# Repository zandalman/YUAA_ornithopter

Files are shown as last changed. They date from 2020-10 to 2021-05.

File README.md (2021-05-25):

# YUAA Ornithopter Project

An ornithopter is a flying machine that generates thrust and lift by imitating the flight of birds. Ornithopters have the advantages of maneuverability, versatility, and stealth over traditional aircraft, making them useful in aerial reconnaissance, search & rescue, and agricultural surveying. In this project, we design and build an ornithopter capable of sustained flight and maneuvering.

# Software

## Controls

Our ornithopter is highly customizable, with many adjustable variables to cater to various flying styles. Such include:

 - **maxFrequency**: Maximum flapping frequency reached when throttle is pulled all the way up. The higher the value, the faster the wings flap, and the more sensitive the flapping frequency will be.
 - **zeroThrottleAngle**: Our ornithopter glides when the throttle is set to 0, or a range close to 0 denoted by **deadZone**. This variable adjusts the angle (in degrees) above the horizontal the wing rests at in glide mode.
 - **levelAngle**: Angle above the horizontal at center of flapping cycle.
 - **maxAmplitude**: How far above and below **levelAngle** the wing flaps.
 - **maxRollPhaseShift**: Roll is achieved by adding a phase delay to the wing opposite to the side of which you want to turn. This variable defines the maximum phase shift when the magnitude of the roll control is at its maximum.
 - **maxPitchAngle**: Pitch is elevated by raising the **levelAngle** and lowered by decreasing it. This variable denotes the maximum change to **levelAngle** when pitch is set to its maximum magnitude. The higher this is, the more sensitive the pitch control.
 - **maxYawAngle**: Yaw is achieved by lowering the **levelAngle** on the side you yaw towards and raising it on the opposite side. This variable defines the maximum deviation to **levelAngle** when yaw is set to its maximum magnitude. The higher this is, the more sensitive the yaw control.
 - **deadZone**: For every control, there is a range in which the value is interpreted as 0. This allows for gliding and makes it easy to keep a purely level angle. The higher this value is, the larger that dead zone.
 - **delayTime**: Frequency at which a new control is registered and a new servo output is generated. The lower this is, the smoother the controls.

All other parameters should be left unmodified.

## Behind the Scenes

The remote controller has 8 channels, each mapped to a control (roll, pitch, yaw, etc.). For each of the controls, we normalize the digital input to a value between 0 and 1 or -1 and 1. There are three control modes—normal, amp, and basic—that reconfigure the layout of the controls. Every iteration of the event loop, we input the controls into a function called **updatePosition()**, which renders new servo positions corresponding to the positions in the flap cycle. **updatePosition()** is a void function, meaning it directly updates the global variables instead of returning an output. The function relies on a unit circle methodology, where the wing position is the *sin* of a rotating point around a circle, and the linear velocity of the rotating point is determined by the throttle. The other controls module the angle and phase.

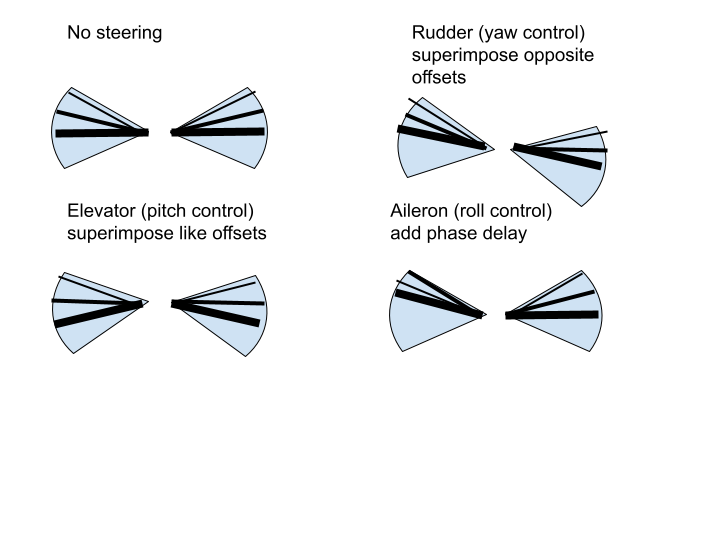
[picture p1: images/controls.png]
Controls


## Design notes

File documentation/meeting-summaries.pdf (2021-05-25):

09/20/2020

Group members
- Zack (project leader)
- Theo
- Kai
- Elijah
- … others???

CAD
- We will probably use Autodesk 360
- Collaborative
- Integrates with Autodesk Eagle
- Okay if you don’t have CAD experience; we will teach you

About the ornithopter
- Wingspan will be in the 1’ to 2’ range
- Steering will be done using a tail wing

Ornithopter kits
- We will send out ornithopter kits some time this month
- See ornithopter kits document for kit options
- Open for ideas for personalized kits because the group is relatively small
- We could also start with designing a more custom kit to send

Design questions to answer as a group
- Gearbox vs servos
- Gearbox
■ More mechanically inclined project ■ More power
- Servos
■ More programming inclined project ■ More control/maneuverability

09/26/2020

See the slides titled “Design Considerations”

New group members
- Olivia

How do ornithopters fly?
- Downstroke

- Wings twist to maintain angle of attack for providing thrust
- Upstroke
- Outer wing lies parallel to direction of motion to minimize resistance
- Inner wing still generates lift

Rudimentary sketch

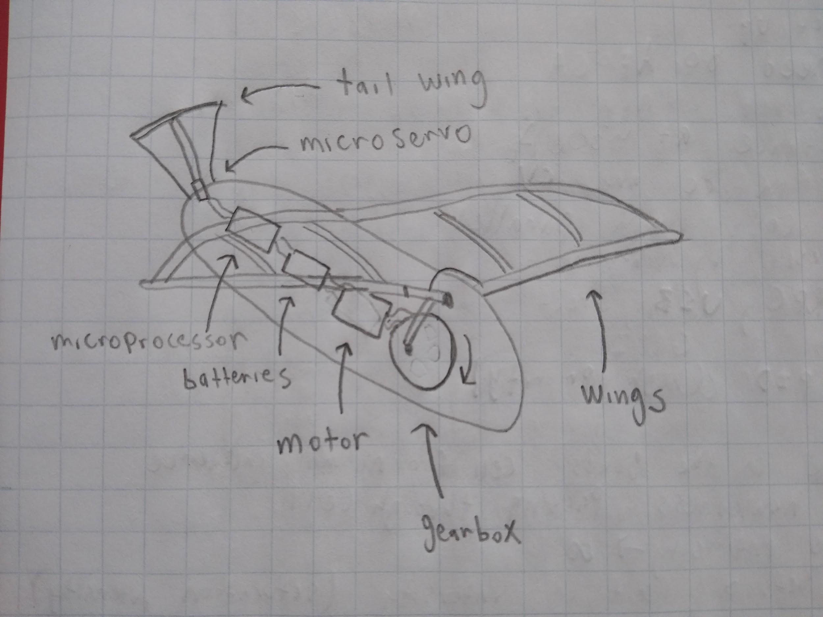
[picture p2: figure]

Electrical components
- Microcontroller (Arduino nano)
- LiPo battery
- Servo
- Brushless motor
- Electronic speed control (ESC)

Mechanical components
- Wing spar (carbon fiber)
- Wings (ripstop or nylon)
- Gear box (transverse gear shaft)
- Frame (carbon fiber)

Kits
- Olivia wants the electronics kit

Tasks

- Olivia will look into necessary software
- Theo will mock up a gear design

Meetings
- We probably need to find a better meeting time
- Weekday schedules are more consistent than weekend schedules

General plans
- Each person will build their own basic ornithopter from kits
- Then we will each work on parts of the preliminary design
- Over winter break, we will consolidate the parts into a full ornithopter

10/04/2020

New group members
- Elsa Durcan
- Bill

Installing Autodesk Fusion 360
1. Go to this link. (https://www.autodesk.com/education/edu-software/overview?sorting=featured&page=1)
2. Click ‘Get Started.’
3. Follow the steps to create an Autodesk account.
4. Install Autodesk Fusion 360 and log in with your account information.
5. Let me know your email so that I can invite you to join the ornithopter project.

Design considerations
- We have decided on the servo method ornithopter

Budget
- We have a lot of money
- ~$3000
- We shall spare no expense!

Materials to send out
- Arduino kit
- Micro servos
- Materials to build the Freebird ornithopter (see resources page)
- Should be able to get materials to everyone in ~2 weeks

Tasks
- Servo software
- Create the Arduino software that will control the wing servos
- Electronics

- Use Autodesk Eagle to design a custom PCB
- Arduino nano
- Gyroscope
- Servos
- Frame
- Create a lightweight ornithopter frame
- Initial prototypes will be 3D printed, but later carbon fiber
- Servos and electronics should mount to frame
- Wing design
- Material
- Wing shape
- Where to place wing spars
- Simulation
- Aerodynamics simulations
- Analytical models
- Testing
- Design a testing rig for future prototypes
- Ornithopter attaches to lever arm for testing thrust
- Force sensor for testing lift

Sorry that I sounded like I was dying today!

10/11/2020

New group members
- Erick

Github
- We have a project github (https://github.com/zandalman/YUAA_ornithopter)
- Commit often and with meaningful messages
- Let me know if you don’t know how to use github and I can teach you

Freebird ornithopter
- Watch video in resources tab
- Parts will hopefully arrive in 1-2 weeks

Parts
- We will probably use
- Servo (https://www.servocity.com/hsb-9370th-servo/)
- RC controller
(https://www.racedayquads.com/products/flysky-fs-i6-6ch-2-4ghz-rc-transmitter-w-ia6-rx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 (https://www.racedayquads.com/products/flysky-fs-i6-6ch-2-4ghz-rc-transmitter-w-ia6-rx?variant=31607739383921)

VjFQtWn2D6Cq5RWLeTxrtjhKH7ACsuyGcYTnIrtvQOSKdmMEaAvhNEALw_wc
B) (https://www.racedayquads.com/products/flysky-fs-i6-6ch-2-4ghz-rc-transmitter-w-ia6-rx?variant=31607739383921)
- Accelerometer/gyroscope (https://www.adafruit.com/product/4692)

Simulation
- Still need to decide simulation software
- Matlab/simulink (https://www.mathworks.com/help/aeroblks/aerodynamics.html)
- Autodesk CFD
(https://www.autodesk.com/products/cfd/overview?_ga=2.186200874.2037225500.1602 442768-2115175104.1601829206) (https://www.autodesk.com/products/cfd/overview)
- SimScale
(https://www.autodesk.com/products/fusion-360/blog/simscale-launches-engineering-simulation-integration-autodesk-fusion-360/) (https://www.autodesk.com/products/fusion-360/blog/simscale-launches-engineering-simulation-integration-autodesk-fusion-360/)

One-on-one meetings
- If you have any questions or don’t know how to do something, we can arrange a 1-on-1 meeting
- Or if its something quick you can just messages me

Task channels
- Each task has its own channel in the Discord
- Use task channel to collaborate on tasks

Starter task assignments
- Olivia - software
- Bill - electronics
- Erick - wings
- Elsa - frame
- Kai - simulation

10/18/2020

Grant applications
- See in Google Drive
- Examples in case you are interested in becoming a YUAA project leader at some point

Electronics
- 5 V LiPo battery will last longer than a 9 V LiPo battery and will not require a regulator

Simulation
- AmSys and SimScale both provide educational licenses
- SimScale is hosted online and is more lightweight
- SimScale may be better for our purposes

- STP files are a universal 3D model file format that will probably work between different softwares

Parts
- We can finally order parts for the ornithopter
- Will send rubber band powered ornithopter parts to everyone
- Will send Arduino kit to everyone
- Will Bill teensy and gyroscope
- Will send Olivia servo arm, gyroscope, and RC controller
- Will send Erick carbon fiber wing spars

10/25/2020

General
- Reach out to me to set up a one-on-one meeting about advice for your specific task

Grants
- CT Space Grant submitted!

YUAA Talk
- Upcoming YUAA talk at 6 pm EST, Friday November 6th by NASA engineer Brandon Lloyd

Arduino Kits
- Arduino kits have arrived
- Distributing Arduino kits at 4 pm today at Cross Campus
- Unboxing video
- Kit includes Arduino, multimeter, USB cable, breadboard, battery, resistors, micro servo, and more
- Remember to always measure voltage in parallel and current in series with the multimeter
- Recommend trying LED tutorial to get used to Arduino https://www.arduino.cc/en/Tutorial/BuiltInExamples/Blink

Electronics
- Either attach RC receiver directly to the PCB or attach it with an IDC cable
- Gyroscope must use SDA and SCL ports on Arduino, only ports which support I2C protocol
- Will order RC system and gyroscope soon

Simulation
- Generative design is built into Fusion and will be useful for modelling wings
- Look into various wing shapes and wing spar layouts

- Possible meeting with Larry Wilen to discuss aerodynamics

11/01/2020

YUAA Talk
- Upcoming YUAA talk at 6 pm EST, Friday November 6th by NASA engineer Brandon Lloyd

Orders
- New order forms have recently been submitted
- See purchase list spreadsheet for more details
- Phoenix ornithopter kit (https://www.gyroscope.com/d.asp?product=PHOENIX)
- PVA glue for ornithopter kit
- Absolute orientation sensor
- Teensy
- RC transmitter and receiver
- Servos

GitHub
- Olivia, Bill, and Kai are now collaborators
- Download repo: git clone https://github.com/zandalman/YUAA_ornithopter.git
- Add changes to current commit: git add FILENAME
- Remove file from git tracking: git remove FILENAME
- Commit changes: git commit -m “DESCRIPTION_OF_CHANGES”
- Push changes to remote repo: git push origin HEAD (HEAD is an environment variable which represents the current branch)
- Update local repo: git pull origin HEAD
- New branch: git checkout -b BRANCH_NAME
- Switch branches: git checkout BRANCH_NAME

Fusion
- Create a sketch
- Add points
- Connect points with lines to create a shape
- Extrude shape
- Fillet edges to make smooth
- Create a new design to combine multiple other designs
- Use joints to connect different components

Simulation
- Kai has gotten SimuLink working
- Create a wind tunnel out of a rectangular prism
- Equal mass of air flowing into front and out of the back

- Zero air flowing through sides (approximation)
- Trade off between size of wind tunnel and computational complexity
- Suitable for simulating frame + attachments + tail wing
- Doesn’t work for simulating wings
- Determine optimal frame angle

Frame
- Elsa will complete S1 robotic bird frame design on Fusion
- Frame length is 900 mm (approximately 36”)
- Connect servos to frame
- Create holes in frame to decrease weight
- Frame attachments include PCB, battery, servos, tail wing
- How far along the body should the center of mass and the Servos be?
- How can we position the frame attachments so that the center of mass is not too far to the side?
- 75mm to 1” scale of S1 robotic bird frame

●

Wings

- Erick will complete the S1 robotic bird wing design in Fusion
- S1 robotic bird wings

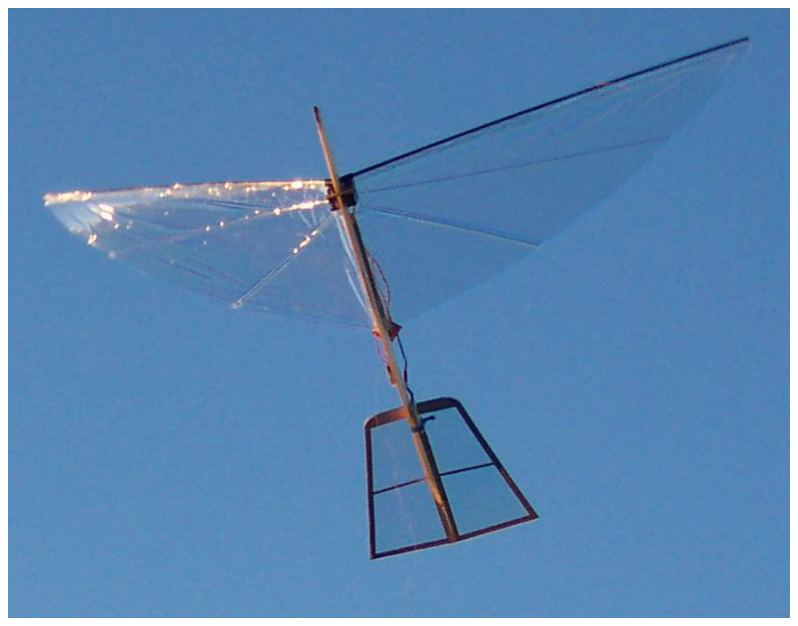
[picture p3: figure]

Electronics
- Bill has finished finding all the electronics parts
- Bill will begin creating connections on the PCB
- RC controller can probably be directly attached to the PCB

Software
- Olivia has written preliminary code for controlling the wings
- 6 channels on the RC receiver: 2 for each joystick and 2 sliders
- One possible configuration is one joystick for amplitude modulation and another joystick for frequency modulation

11/08/2020

Materials
- Kits have not arrived yet but are still on their way
- Glue for kits has been distributed to all on-campus team members
- Bill has a teensy
- Olivia and Bill have orientation sensors
- Olivia has the RC controller
- Erick has his Arduino kit

Electronics
- Servos take 6 - 7.4 V
- Teensy takes 3.3 - 5 V
- We need a step-down buck converter (https://www.adafruit.com/product/1385)
- Each servo pulls up to 2 amps (stalls at 2.1 amps) (https://hitecrcd.com/products/servos/digital-brushless-servos/hsb-9370th-multi-purpose-brushless-titanium-gear-servo/product) (https://hitecrcd.com/products/servos/digital-brushless-servos/hsb-9370th-multi-purpose-brushless-titanium-gear-servo/product)

- We need a high-amperage 7.4 volt battery (possibility https://www.maxamps.com/rc-battery-lipo-6500-2s-rc-7-4v-battery?gclid=Cj0KCQiAy579 BRCPARIsAB6QoIYKOQVezT03-l3f8dImmDQwtt1hdDrGO9Lj5xLm6FgBuSWlyKX10Xc aAuH7EALw_wcB) (https://www.maxamps.com/rc-battery-lipo-6500-2s-rc-7-4v-battery)
- RC receiver can either mount directly on the board or be connected via an IDC cable

Frame
- We need to mount the servos sideways so that they can flap the wings

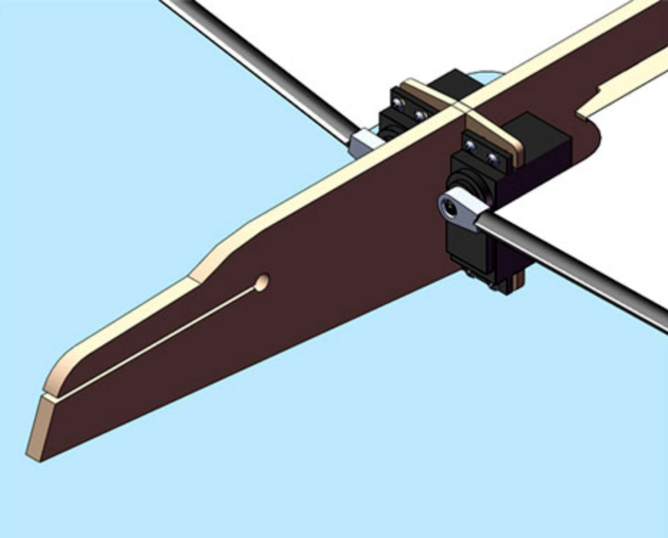
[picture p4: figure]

- We will need a separate piece which fits into the frame
- This piece could potentially include a more aerodynamic cover for the servos

Wings
- Discount photoshop website (https://pixlr.com/x/)
- Erick will design the wings in Fusion
- 67” wingspan, translates to 1675 mm in our design

Simulation
- Kai successfully ran an aerodynamics simulation of a simple stp file
- We will set up a meeting with Larry to talk about aerodynamics
- Simulation tests on more complex and 3D frame design
- Holes vs no holes
- Aerodynamic cap for servos?
- Try using a smaller box for the simulation to speed it up

Software
- Successfully controlling micro servo using Arduino
- Olivia will test code for orientation sensor

11/15/2020

CAD tips
- Use McMaster to find CAD files for parts like nuts and bolts (https://www.mcmaster.com/)
- Go “back in time” to edit sketches and other design elements

Wings
- The robotic bird website claims that for the servos we are using, 1.2 meters is the optimal wingspan (https://www.the-nref.org/content/building-robotic-bird)
- Benefits of the shorter wingspan include longer and faster flight
- The original wingspan of the S-1 robotic bird design was 1700 mm. The new wingspan is 1200 mm. Therefore, we can scale down the wingspan by a factor of about 1.4.

Frame
- CAD design now includes pieces for the servos to mount which wedge into the frame
- We can also scale down the frame length to match the shorter wingspan
- We cannot scale down the frame height because the frame is already about the height of the servos
- The original frame length is 900 mm. After scaling down by a factor of 1.4, the new frame length is 650 mm
- We will use the custom servo arms from BirdKit.com to connect the servos to the wings (http://www.birdkit.com/robotics.parts.html)
- Servo datasheet
(https://hitecnology.com/images/products/pdf/7_HSB-9370TH_Drawing-2017.pdf)
- The servo arms fit with BirdKit.com’s hollow carbon fiber spars (http://www.birdkit.com/robotics.spars.html)
- Dimensions for the wing spars are given by Goodwinds, which appears to sell the same product for a higher price (https://goodwinds.com/product/wct-sky-shark-3pt-32-5/)
- The wing spar is in the CAD design. For the shortened wing span, we will need to cut off the wing spars
- Hollow wing spars will save weight over solid wing spars

Center of Mass
- We will use the frame design to fix the center of mass
- We will mount batteries, PCB, and other items to maintain the center of mass set by the frame
- We can calculate the pitch of the ornithopter in flight based on the distance between the center of mass and the servos
- Battery weighs 42 grams
- Servos weigh 68 grams each
- PCB will probably be lighter than the batteries

Simulation
- Kai is running a simulation on the updated frame design

Software
- Olivia is working on getting the RC system connected to the micro servo

11/29/2020

Software
- Olivia can read inputs from the RC receiver
- Gyroscope giving garbage data
- Maybe gyroscope needs to be calibrated

Frame
- Ornithopter should fly at 20 to 30 degrees off the horizontal
- Tail wing is 10 to 15 degrees off the frame
- Center of mass on weird ornithopter video guy’s ornithopter is very far forward
- Skeptical about his claims
- Fusion can calculate center of mass
- Must insert correct density from frame material
- Calculate center of mass for frame alone. Include other parts of calculation afterwards
- Elsa will upload design files from weird ornithopter guy’s webpage

Wings
- Zack working on implementing wing design in Fusion

Electronics
- Bill has created a prototype of the board design

12/06/2020

General
- Optional meeting next week

Frame
- Aerodynamic cap
- Attached to servo mounting screws?
- Needs side hole for wings
- Which shape is the most aerodynamic?

Electronics
- Bill finished board design
- Fits nicely on ornithopter frame

- 4-40 screws in corners
- Need to switch servo connections to other side of board so that they are closer to the servos on the ornithopter
- Need to choose 3 x 1 pinhead on RC receiver connections with smaller pads
- Bill has soldering equipment and can solder and test the board over break

Wings
- Wing design fully implemented in Fusion
- How to attach the tail wing to the ornithopter?

Simulation
- Kai and Zack met with Larry Wilen
- Use the scientific method to get full use of aerodynamics simulation
- Get total drag as a single number
- Use simplified version of ornithopter for testing
- Use software to make comparisons, because it can’t be fully trusted quantitatively
- Tilt ornithopter at an angle
- Try different wind speeds
- Servos are causing a lot of drag

01/10/2021

Generel
- Hope everyone had a nice holiday season
- We will start putting the ornithopter together this semester!
- Will be sending out a Facebook post to recruit sophomores to group
- Feel free to reach out to me if you want to help in recruiting
- Applications for YUAA Eboard will open soon
- Happy to give advice for the applications
- All of you would make great project leaders, outreach directors, etc.

Ornithopter kits
- Zack and Erick have built ornithopter kits
- They are really cool!

Electronics
- Test circuit on breadboard before doing any soldering
- Send Bill step-down converter, batteries, and Servo
- Bill needs code from Olivia; can collaborate to figure something out

Wings
- Erick will build the wings over break
- Wing design complete in Autodesk Fusion

- Can use Canvas feature in Fusion to
- Send Erick ripstop nylon and carbon fiber wing spars
- Erick is driving to campus in the spring, so sending him stuff is no problem
- Carbon fiber rods will slide into pockets in the wings (like a tent)
- Anyone know how to sew?

Frame
- Theo will 3D print parts for the frame to make sure that they fit together
- An option for our final design: use a company to professionally manufacture custom carbon fiber parts (Custom carbon fiber parts http://www.protechcomposites.com/custom-orders/)
- Theo and Bill have 3D printers

01/17/2021

General
- YUAA pre-interview questions now available in Discord
- Application due February 28th
- Reach out to me with questions or for brainstorming
- There will be whiteboarding sessions coming up soon

Frame
- Theo will 3D print parts for testing
- Gap in frame is 5 mm wide

Electronics
- Bill has received the Servo and step-down converter
- Zack will upload a PDF of the servo instructions
- Servo comes with a PAD, which we might want to use to help the step-down converter handle back currents

Software
- Zack will create a simple version of the code for electronics testing purposes

Wings
- Wing materials have been shipped to Erick and should arrive soon
- Carbon fiber tubes, 3 mm carbon fiber rods, and duralar from Birdkit.com

Simulation
- Kai will run some ornithopter simulations with the wings
- Test different tail wing configurations, angles, sizes, etc.

01/24/2021

New group members
- Aliza

Frame
- Standardize widths to ⅛’ or ¼’ for easier laser cutting ability
- Need to make pieces slightly small to allow for manufacturing defects
- Interlocking u-shapes for servo mount to frame connection
- Prevents side-to-side motion
- Shorten slots along vertical direction so servo mount pieces can stay the same size
- For first prototype, glue alone might work
- To mount tail, create a hole in the rear of the ornithopter
- Create a hole for the battery to allow battery to be in-line with the center of mass

Electronics
- Servo works with Arduino
- How many rotations per second can we get at 60 degrees of rotation?
- Figure out how PAD works
- Get Teensy working
- Test step-down converter using multimeter

01/31/2021

ISC Conference
- Register at https://tinyurl.com/IvySpace4
- It’s free and there is no obligation to attend once you register

CEID
- Sign up to be a CEID member
- Go to https://yaleconnect.yale.edu/student_community?club_id=38455
- Click “Join”
- Check the checkbox and click “Join” again
- Do the laser safety training (https://ehs.yale.edu/trainings/embedded-laser-safety-program)
- At some point, events will start appearing under the CEID page on Yale connect
- You will be able to sign up for a laser cutting tutorial
- 3D printing tutorials could also be helpful, but not necessary

Frame
- Updates to the frame from last meeting have been made
- How do we keep the battery in the battery hole?
- Adjust thickness of carbon fiber above tail wing slot to 1/8”
- Possibly adjust thickness of frame to 3/16” rather than 1/8”

- In a future design, add a mechanism to adjust tail wing angle before flight
- For now, simplicity is better

Simulation
- Simulate ornithopter at different body angles and tail wing angles
- Zack will send Kai STP files

Electronics
- RC receiver will not be soldered to the board
- Instead, 8 male-to-female cables will go from the board to the RC connector (6 channels + GND + VCC)
- Zack created custom device in Autodesk Eagle for switch
- Ship Aliza an Arduino kit (Franklin college)

Wings
- Changed address for duralar material
- Working on changing address for wing spars

02/07/2021

CEID
- Go here do get all the info about doing CEID training (https://yaleconnect.yale.edu/student_community?club_id=38455&menu=blog)
- Laser cutting certification requires 4 steps
- Complete laser safety training
- Complete embedded laser safety training
- Email training certificates to CEID
- Complete CEID laser safety training
- Also a good idea to do the makerbot training

Electronics
- Bill tested Teensy, step-down converter, gyroscope, and servo working together
- Bill will add the switch to the PCB
- Bill will replace the through hole array with 8 pins
- May use a smaller version of the RC receiver (https://www.amazon.com/Flysky-FS-A8S-Receiver-i-BUS-Transmitter/dp/B0761N3FFC)
- Can be paired with our RC transmitter (see https://www.amazon.com/Flysky-FS-A8S-Receiver-i-BUS-Transmitter/dp/B0761N3FFChttps://www.youtube.com/watch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)
- Will send Olivia the small receiver to test
- Big boy battery has arrived, very powerful and a little scary

Software

- Smaller receiver uses IBus protocol (developed by Flysky) which carries all channels in one digital signal
- There are Arduino libraries to decode with IBus protocol (https://www.arduino.cc/reference/en/libraries/ibusbm/,https://www.arduino.cc/reference/en/libraries/ibustrx/)

Wings
- Duralar has arrived, wing spars are on their way
- Use sewing to create sleeves in the wing
- Aliza has some sewing experience
- Erick will go over video and write down steps for wing construction procedure (https://www.youtube.com/watch?v=ufjvmdAXyZs)
- Use tape to make wing more stiff at wing spar sleeves

Simulation
- Current design may be too complex for simulation to work
- Zack will send a more abstracted version of the design to Kai to test

Frame
- Hold battery in place using zip ties and small holes in the frame
- Inspiration taken from https://www.thingiverse.com/thing:1324260
- Similar set-up could work for receiver if smaller receiver doesn’t work

02/14/2021

General
- Happy Valentine’s Day
- Apply for Eboard positions!
- The application questions are uploaded to the google drive

Simulation
- Abstracted design still did not work
- There may be a problem with the intersection of the wing spars and the wing material in the design
- Zack will send Kai an updated design

Frame
- Triangular holes instead of square holes in frame
- Need to fillet the edges of the holes
- Basswood is on its way to the CEID
- Unlike plywood, basswood takes a larger load parallel to the grain vs perpendicular to the grain

- We should have the grain go vertically along the frame because most of the load from the servos will be vertical

Wings
- Before mounting the wings on the servos, we should set the servos into a position in the middle of their range
- Erick, Aliza, and I will meet in the CEID this week to discuss the wings
- Erick has the procedure for creating the wings

Testing rig
- For a first pass, we can use a vice to clamp the ornithopter to a table
- Eventually, we may want a more complex design which can incorporate a force sensor

Electronics
- Bill finished the PCB design
- Zack will place the order for the PCB board
- May have to order from an American manufacturer to avoid funding restrictions about Chinese manufacturers

Software
- Bill will share how to read data from the gyroscope with Olivia
- The left stick on the RC controller will be for steering and the right stick will be for throttle
- For now we will ignore the horizontal position on the right stick and the vertical position on the left stick
- Olivia will work on implementing the throttle functionality
- Find the default reading when the right stick is in the neutral position
- Create a linear map from the difference between the current and default readings to the flap frequency
- Max flap frequency of 7 Hz
- Possibly include a “buffer zone” around the neutral position of the right stick where nothing will happen to avoid accidentally triggering the throttle
- Example code
float normalizedReading = abs(currentReading - defaultReading) / (maxReading -defaultReading);
float frequency = normalizedReading * maxFrequency;
float delay = (1000 / frequency) / 2; // divide by 2 because each cycle has two servo commands, up and downt
- The servos should rotate through an angle of 45 degrees, with 15 degrees acting as a “neutral” position
- When the new RC receiver arrives, Olivia will test it

02/21/2021

Simulation
- New frame design is not working in Simscale
- Holes in the frame could be the problem

Frame
- Erick 3D printed the servo mounts
- May have to 3D print a second time because the supports are attached tightly
- Test servo mounts in CEID
- Still waiting for basswood

Wings
- In the CEID, Aliza and Zack worked on the wing
- Half the wing is complete, we will finish the other half next week
- Going to the CEID on Thursday @ 2:30 pm
- Finish wings in CEID
- Use superglue or gorilla glue to fix the wing spars onto the custom servo arms

Electronics
- PCB has not arrived yet
- Solder teensy on top of male-to-female connectors for ease of detaching and programming
- Still waiting for mini RC receiver

Software
- Zero position of the servo is only relevant insofar as we want the full range of motion of the servos
- Servo arms can be detached and reattached at any angle
- Throttle mechanism is up and running
- Code needs to be commented to make readable
- We need a simple version of the code for basic testing in the CEID this Thursday
- Input a frequency
- One servo flaps in a sinusoid at that frequency
- Look up table for sine and inverse sine functions
- One servo rotates clockwise, another servo rotates counterclockwise. Therefore, different signals need to be written to each servo
- When throttle is zero, wings should default to 15 degrees above the horizontal
- Rudder and elevator steering mechanisms should work in the same way
- Three steering mechanisms (in order of importance)
- Rudder (yaw) - superimpose flapping with positive offset on one wing and negative offset on the other
- Elevator (pitch) - superimpose flapping with a positive or negative offset on both wings
- Aileron (roll) - add a phase shift to the flapping

- Olivia will figure out what the usual mapping for steering to channels is
- Bill and Kai will join Olivia in working on the code
- Code can be broken up into implementing look-up table, working on steering, and working on IBus protocol decoding

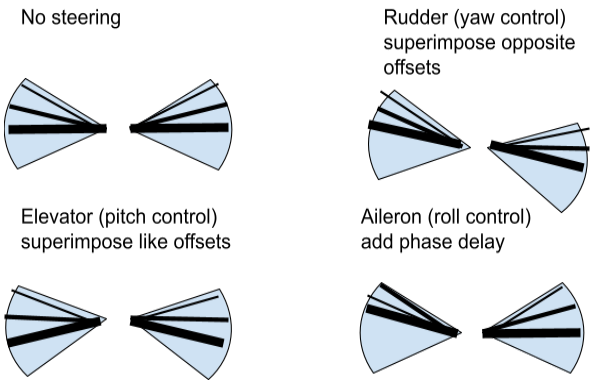
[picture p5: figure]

02/28/2021

General
- Apply to Eboard positions
- Deadline for applications will probably be extended
- You can apply for non-project-leader positions and still be a part of the project

Software
- Olivia made an excellent summary of the code and its current problems (https://docs.google.com/document/d/1VA-EAru0-6IPIT6ASaZQ7ZtNaGr3ZuQab4mmbTLjAoA/edit?usp=sharing) (https://docs.google.com/document/d/1VA-EAru0-6IPIT6ASaZQ7ZtNaGr3ZuQab4mmbTLjAoA/edit?usp=sharing)
- The ‘writePos’ function is taking 150 ms for some reason
- sin and asin functions can be sped up by using the fast trig library
- Search for fastTrig in the Arduino library manager
- Add the line #include "FastTrig.h" at the top of the script
- Replace sin and asin with isin and iasin
- Declare specific pin numbers as global variables at the beginning of the file

- Possibly get rid of four loops with only two iterations (but maybe not if it’s not the source of the slowdown)
- To determine the source of the slowdown, remove levels of complexity until the slowdown disappears
- Aliza will help implement steering functionality
- In the future, we can detect when we are in freefall and implement an overriding behavior to try to save the ornithopter

Wings
- Wings have been completely cut out of duralar
- Servo + custom servo arm + wing spar apparatus is working perfectly
- Zack will reach out to the CEID for guidance on cutting wing spars
- Inhaling carbon fiber dust is extremely dangerous
- Will have to cut wing spars outside of CEID
- Use a wet paper towel and a razor blade (https://www.flitetest.com/articles/how-to-cut-carbon-fiber-rods)
- Zack will order extra wing material just in case
- We will go into the CEID this Thursday at 2:30 pm

Frame
- Custom servo mounts fit servos
- Wood still has not arrived
- Ian said that there may be wood we can use in the aerospace room
- Zack will contact Ian to find a time to meet in the CEID and look for wood

Electronics
- Bill received the PCBs
- Teensy does not lay flat on connectors; Bill will have to sand the side of the connectors
- Don’t sand the top of the connectors (from personal experience)
- Attach male connectors everywhere
- Step down converter will hang down off of the PCB
- Bill will keep orientation sensor with him so that he can do tests with it to help with software
- Bill can just check the connections to the orientation sensor without soldering since he has already tested it
- Switch is not flush to the PCB, but it’s not a big deal

Simulation
- Frame without holes worked, which indicates that the problem has something to do with the holes
- Kai will test the frame design with one hole as a check

03/07/2021

General
- Last day for Eboard applications
- Check email for YUAA t-shirt and jacket order form

Frame
- Steps to get laser cutter certified
- Yale Laser Safety Awareness Training (https://ehs.yale.edu/laser-safety-training)
- Yale Embedded Laser Safety Training (http://ehs.yale.edu/training/embedded-laser-safety-training-ceid-personnel)
- Safety training checklists should be accessed through http://www.yale.edu/training/ and may be taken online. Please save the quiz transcript post-completion and email it to ceid@yale.edu
- Basswood has arrived
- Will laser cut the frame this week

Wings
- We cut 4 of 6 wing spars last time at the CEID; will cut remaining two wing spars next time
- Mudi mentioned a strategy for attaching the win spars while maintaining tension in the wing
- Zack will discuss with Mudi privately

Software
- Mini RC receiver has arrived
- Olivia will work on binding RC receiver to RC transmitter and decoding IBUS signal
- Kai will work on implementing the steering system
- Zack and Kai will meet to discuss the code

Electronics
- Soldering of the PCB is almost complete
- When soldering is complete, Bill will send the PCB to Yale campus
- Package carefully and don’t forget to send the servo as well
- PCB will probably be incorporated into the second ornithopter prototype

03/14/2021

General
- Happy pi day!
- Make sure to fill out YUAA t-shirt order form
- It’s okay to prioritize midterms over ornithopter!

Frame

- Frame is finally laser cut
- Frame design is slightly longer than 24” (the length of our wood) so we had to cut in two pieces
- For the final ornithopter iteration, we will order a long piece of carbon fiber so we don’t run into the same problem
- We can attach the pieces together with glue and possibly with short CF struts
- Tasks for next time in the CEID
- Attach the frame pieces together
- Attach the tail wing to the frame with glue
- Attach the battery to the frame with zip ties
- Attach the servo to the frame
- Attach the RC receiver to the frame
- Aliza will get laser cutting trained this week

Wings
- Tail wing is small; maybe next iteration we can make a larger tail wing
- Next time in the CEID we will attach the duralar to the tail wing piece (https://www.youtube.com/watch?v=wipw5tMYNWM)
- We will wait until we have both servos before we attach durular to main wings

Software
- Mini RC receiver is working
- Requires a manual installation of a library into the Arduino IDE (https://github.com/Nikkilae/PPM-reader)
- For roll, pitch, and yaw, we will update the position function every cycle under the assumption that the joysticks are being moved smoothly
- For throttle, we will update the position function only when |sin(2pi * frequency * t)| < epsilon. Note that we ignore phase shift

Electronics
- Bill will solder the orientation sensor onto the PCB and we will send him a replacement
- The PCB is almost complete and Bill will ship it early this week
- Bill will be reimbursed for shipping costs
- Use lots of packaging to keep parts from getting damaged

03/21/2021

General
- Timeline (tentative)
- April 1st
■ Finish first ornithopter iteration
■ Finish minimal working version of code with steering and RC control
- April 15th

■ Finish second ornithopter iteration
■ Finish polished version of code with steering and RC control
- April 29th
■ Finish final ornithopter iteration
■ Test launch
■ Finish minimal incorporation of orientation sensor data into code
- May 10th (approximately)
■ Finish code adjustments
■ Final launch!

Electronics
- PCB and servo are shipped and should arrive by Monday
- Zack will order an extra orientation sensor for Bill
- Olivia will hold on to the RC equipment for the time being
- Now that electronics are basically done, Bill will shift over to the software side of the project

Software
- Olivia will make a very simple sketch which flaps both wings simultaneously (for testing purposes)
- Incorporate gyroscope into code
- Critical angle for roll, pitch, and yaw
■ As the ornithopter gets closer to some critical angle, we will dampen steering in that direction
■ For example, if the ornithopter is rolled far to the left, attempts to roll further to the left by the user will be ignored
- Fail safe for falling
■ When the acceleration reaches close to 9.8 m/s

2
, we will override user
control to either
- Position the wings optimally to prevent damage upon hitting the ground
- Restore flight
- To prevent people from waiting on each other to implement the steering, we will have a “whoever gets to it first” policy
- Make sure to put a blurb about what progress you made in the Discord
- For questions about software, use the software channel in the Discord so everyone can read / answer the question

Frame
- All pieces fit together spectacularly in the frame
- Zip Tie method for battery works well
- Aliza will go into the CEID to attach the tail piece to the main ornithopter frame

- Second ornithopter iteration will have larger tail wing (scaled by 1.5 x) and a hole which properly gives room for the Lipo battery wires

Wings
- Aliza put together the tail wing using the method discussed last week

03/28/2021

General
- We will try to complete our first prototype this week!

Frame
- Purchased carbon fiber with foam core material for ornithopter frame (https://dragonplate.com/carbon-fiber-prepreg-last-a-foam-core-sheet-0125-x-24-x-36)
- Foam core is ⅛”, so foam core with carbon fiber plating will be slightly thicker than our current design
- Not a bad thing because current frame has been a little shaky when the servos are going at 7 Hz

Software
- Kai updated the control software
- Each timestep, an angle delta theta is added to the argument of the sine function
- The size of delta theta will depend on the throttle
- Kai will test the updated script on the servos
- Bill will work on implementing the gyroscope in the code
- The first step will be making a circuit which flashes an LED when the magnitude of the linear acceleration gets close to free fall
- The next step will be making a circuit which flashes an LED when the gyro is tilted at a certain angle
- Keep in mind that the gyro will be oriented sideways on the ornithopter
- The gyro code could include a calibration step
- Get orientation data from the gyro as Euler angles (https://en.wikipedia.org/wiki/Euler_angles)
- Olivia will create a minimal working version of the code using the RC controller (doesn’t necessarily have to have all steering functions yet)
- How should we implement timesteps in the code? Right now we are using the delay function, but maybe we should implement a system that ensures that each loop occurs in a definite amount of time?

Electronics
- Olivia will give Zack the RC equipment for testing on the first ornithopter prototype
- The PCB arrived and fits neatly on the ornithopter frame
- The PCB works perfectly

- Next time, we will attach the RC controller to the PCB

Wings
- This week in the CEID, Aliza and Zack will construct the ornithopter wings
- We will film the wings using a slow motion camera to understand how our design is currently working and where it can be improved

04/04/2021

Software
- Bill created a working code which outputs to serial when the magnitude of the acceleration passes a certain threshold
- Euler angles may have a gimbal lock; should not be an issue
- We can always use quaternions if we need to
- To read two types of data at once, we may have to modify the Wire Arduino library for faster I2C communication
(https://forum.arduino.cc/index.php?topic=410787.0#msg282675)
- Bill will get Euler angles working
- Kai will implement his new control code on micro servos as a proof on concept
- Olivia will create a minimal working version of the RC control code before Wednesday
- Code does not need to have full throttle functionality (i.e. throttle stick can just function as an on-off switch)

Wings
- Created an initial wing design using tape
- Wings were nowhere near as taut as they need to be
- Possible solutions
- Create tension in wings before attaching wing spars
- 3D print a piece to connect all wing spars together
- Make center of wings triangular instead of rectangular
- Poke holes in the wing and attach wing spars to the wing with zip ties
- Aliza and Zack will do more research about common methods for mylar wings

Electronics
- Burned out the buck converter by accidently putting it on backwards
- Not an issue because we have another one
- Zack may solder buck converter directly onto board to avoid future confusion
- Zack will solder connector for RC converter onto PCB

04/11/2021

Wings
- We tried two techniques to make the wings more taut

- The lashing technique: use a thread to tie wing spars togethers and dunk in glue
- The connector technique: 3D print a connector for the wing spars
- We are leaning towards the connector technique because it makes it easier to remove the wing spars after we are done
- Next time in the CEID, we will construct the second pair of wings using the 3D printed connectors
- It is important that the back of the wing is attached to the frame
- Last time, we used a clothes pin. We will probably continue to use a clothes pin because it is convenient and easy to implement
- Another option is to add a hook into the frame design to allow the back of the wings to attach easily

Frame
- We will weigh the frame and send the data to Bill
- Bill will do some back-of-the-envelope calculations to determine how much work we expect to do and compare it to the work required for flight
- Aliza is laser cutter certified
- Aliza will laser cut the second iteration of the frame which includes a larger tail wing and a different hole placement around the battery
- Zack will send Aliza the dxf files for the laser cutting
- We will test the ornithopter by attaching it to a string and letting it execute circular motion
- We may add a hole in the top of the frame to make it easier to attach the string

Electronics
- Zack soldered a crimp connector onto the spare step-down converter
- The leads were too thick for the crimp connector, so Zack needed to solder the leads to smaller leads first and cover up the connections with heat shrink
- The electronics are now completely functional
- We tested the RC receiver and it works

Software
- Kai tested the servo control code on real servos and it worked the first time (a miracle!)
- Kai will work with Olivia to incorporate the RC control into the code
- Kai will add comments to his control code
- Kai may take photos or videos to document his tests on the servos
- The original PPM reader library does not work with Teensy, so we need to switch the code to use a new library which is included automatically with Teensyduino (https://www.pjrc.com/teensy/td_libs_PulsePosition.html)
- Disadvantage of new library is that we may have to read each channel separately instead of reading all channels simultaneously
- Olivia will install Teensyduino to do debugging with new library
- Teensyduino installation instructions (https://www.pjrc.com/teensy/td_download.html)
- Random idea: a switch on the RC controller can flip between different control modes

- Normal mode: joystick channels are frequency, roll, pitch, and yaw
- Amplitude mode: joystick channels are frequency, amplitude, roll, pitch, and yaw
- Manual mode: joystick channels are left and right wing positions
- Bill is still working on Euler angles in orientation sensor
- By making a few assumptions, two of the Euler angles correspond directly with pitch and yaw
- Bill wrote a function which returns a boolean based on whether we are falling or not
- We need to make sure that acceleration measurements are not just noise. We can do this by averaging the sensor outputs over multiple measurements
- When we are falling, we can move the wings to some nominal position and cease flapping

04/18/2021

Wings
- Switched from 3 mm diameter wing spars to 2 mm diameter wing spars for interior wing spars to increase flexibility
- Updated wing design slightly to make attaching interior wing spars easier
- Interior wing spars now lie at 15 and 30 degrees respectively
- Intersection point of interior wing spars and main wing spar is 30 mm from the servo to prevent the spar connector from hitting the servo
- 3D printed new spar connector to account for smaller interior wing spar diameter
- Wing spars fit snugly into the holes in the spar connector, although if new version are required we may want to increase clearance on the holes slightly (current clearance is diameter plus 0.25 mm)

Frame
- Will get frame weight measurement soon
- There was a delay in shipping the carbon fiber foam for the frame, but it should ship by early next week at the latest
- Methods for adjustable center of mass
- Multiple possible battery locations
- Some kind of slider
- We will laser cut new frame design this week

Software
- Bill successfully can read Euler angles for pitch and roll, but not for yaw
- We only need the critical angle feature for pitch and roll, so we can ignore the yaw Euler angle
- RC control and steering functionality are fully implemented
- Kai will add two control modes in the code. One control mode will map roll to channel 4 and amplitude to channel 5. The other control mode will switch roll and amplitude
- Channel 5 is controlled by a knob on the top of the RC controller

- We can switch between control modes by mapping the control mode to a switch on the RC controller

04/25/2021

General
- Zack is giving a 5-minute presentation on the ornithopter on Thursday at the (virtual) YSEA grant recipient annual meeting
- Register here
(https://www.eventbrite.com/e/2021-ysea-annual-meeting-networking-online-event-only-ti ckets-144200787437) (https://www.eventbrite.com/e/2021-ysea-annual-meeting-networking-online-event-only-tickets-144200787437)

Frame
- Carbon fiber has arrived!
- We will wait to laser cut the carbon fiber until we know for sure that the prototype design is capable of flying

Wings
- Ian says there may be extra ripstop nylon in the CEID
- If there is, we may switch from duralar to ripstop nylon
- New wing design was a huge improvement, but the inner parts of the wing are still not taut enough
- New 3D printed parts and new frame design will allow a new bracing wing spar which connects to the back of the frame to be installed

Software
- Euler angle measurements fail to be independent
- Bill will try an approach using quaternions
- Bill will add acceleration kill switch code into the main script
- Kai will add manual kill switch code into the main script
- Kai mapped amplitude to channel 5 and added a second control mode
- To fully implement the control modes, we need to figure out how the switches on the RC controller manifest in the ppm reader

Documentation
- Bill and Kai will update the README.md file on the github with documentation about their work on the software and electronics

05/02/2021

Frame
- Cutting carbon fiber frame at Makehaven this Friday
- Carbon fiber is 4.5 mm thick as opposed to ⅛” thick

- Frame design, including 3D-printed parts, needs to be updated to account for new thickness

Wings
- Ripstop nylon arrived
- Add an additional thicker wing spar near the body of the ornithopter
- This will allow each wing to be constructed individually
- Wings will be connected by a flap of ripstop nylon

05/09/2021

General
- Final meeting
- Thank you everyone for being a part of this group!
- I encourage everyone to join YUAA again next year

Frame
- New frame and tail cut out of carbon fiber using water jet cutter at MakeHaven
- Need to 3D print new parts for servo connectors and screw connectors
- Small parts did not work well with the carbon fiber foam material because the carbon fiber layers break apart

Wings
- New wing design was tested and it works well
- New wings are very stable
- Next time, we will sew a connector flap of ripstop between the wings

Launch
- Soft launch to see if flying is feasible
- If soft launch is successful, we will move to a full launch event
- Launch event will be streamed on Zoom and anyone is welcome to attend
- If soft launch does not go well, I will be here in the summer to tinker with the ornithopter and the launch will occur sometime over the summer

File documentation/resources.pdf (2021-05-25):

https://github.com/zandalman/YUAA_ornithopter
- Ornithopter github

http://www.ornithopter.org/
- Comprehensive ornithopter resource
- How do ornithopters fly? (http://www.ornithopter.org/how.fly.shtml)
- How-to section (http://www.ornithopter.org/how.1.shtml)
- Power systems (http://www.ornithopter.org/how.motor.shtml)
- Gear design (http://www.ornithopter.org/how.gear.shtml)
- Flapping mechanism (http://www.ornithopter.org/how.flap.shtml)
- Wings (http://www.ornithopter.org/how.wing.shtml)
- Stability and control (http://www.ornithopter.org/how.stab.shtml)
- Ornithopter parts seller (http://www.birdkit.com/)
- Example of Servo-type ornithopter (http://www.birdkit.com/robotics.s1.html)
- Example of a gearbox for a gearbox-type ornithopter (http://www.birdkit.com/models.gbx.html)
- Flapping Mechanism Design Tool (http://www.ornithopter.org/software.shtml)
- Software tool for designing ornithopter flapping mechanisms
- How to use (http://www.ornithopter.org/flapdesign.info.shtml)
- Useful for spotting asymmetric flapping or a locking of the mechanism

http://www.ornithopter.de/english/principle.htm
- The physics behind ornithopter flight

https://www.mdpi.com/2226-4310/2/2/235/htm
- Scientifically-driven ornithopter design
- Possible test rig setup

https://www.instructables.com/id/Opensource-Ornithopter-Prototype-Arduino-Powered-a/
- Complete how-to on ornithopter design
- Watch the videos!
- Part I: https://youtu.be/ruWvzF1fGHw
- Part II: https://youtu.be/ufjvmdAXyZs
- Part III: https://youtu.be/pB9SABFNbsA

https://youtu.be/0E77j1imdhQ
- Human-powered ornithopter

http://www.ornithopter.org/archive/freebird.pdf
- Simple rubber-band ornithopter
- Video instructions: https://youtu.be/AF4SqJF6PdA

https://www.the-nref.org/content/building-robotic-bird

- Servo method ornithopter
- Detailed instructions on how to implement flapping with Servos
- How to steer an ornithopter without a rudder by adjusting wings independently

http://www.brendanbody.co.uk/flight_tutorial/index.html
- Useful observations about the flight of birds

https://pages.mtu.edu/~suits/misc/tapsizes.html
Hole sizes for standard screws

Parts

- Servo
- https://www.servocity.com/hsb-9370th-servo/
- RC controller
- https://www.racedayquads.com/products/flysky-fs-i6-6ch-2-4ghz-rc-transmitter-wia6-rx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 (https://www.racedayquads.com/products/flysky-fs-i6-6ch-2-4ghz-rc-transmitter-w-ia6-rx?variant=31607739383921)
- https://imgaz.staticbg.com/images/upload/2014/04/FS-i6%20Maniac.PDF
- Accelerometer/Gyroscope
- https://learn.adafruit.com/adafruit-bno055-absolute-orientation-sensor/arduino-co de (https://learn.adafruit.com/adafruit-bno055-absolute-orientation-sensor/arduino-code)

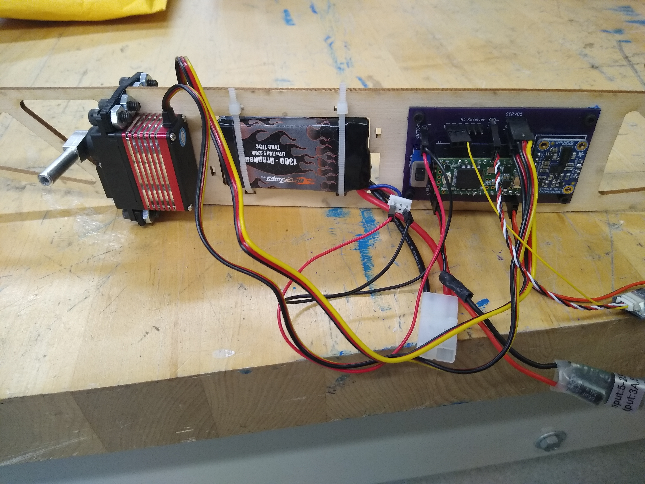
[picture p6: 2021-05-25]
images/electronics.jpg

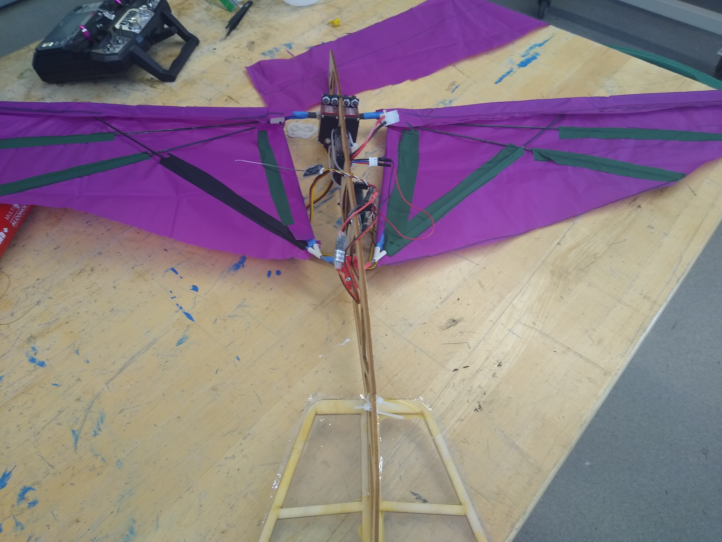
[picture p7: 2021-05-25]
images/wing-design.jpg

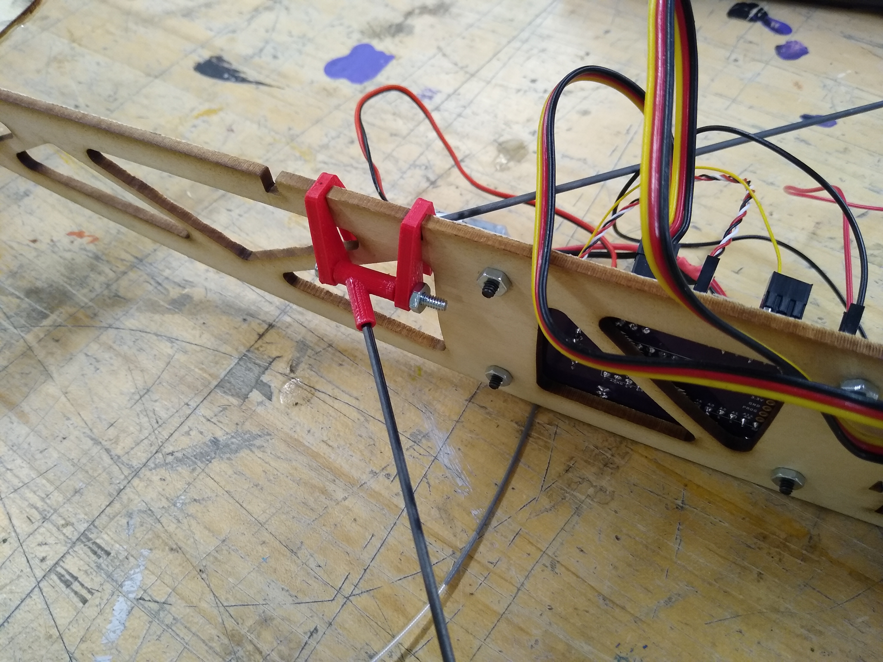
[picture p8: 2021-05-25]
images/screw-connector.jpg

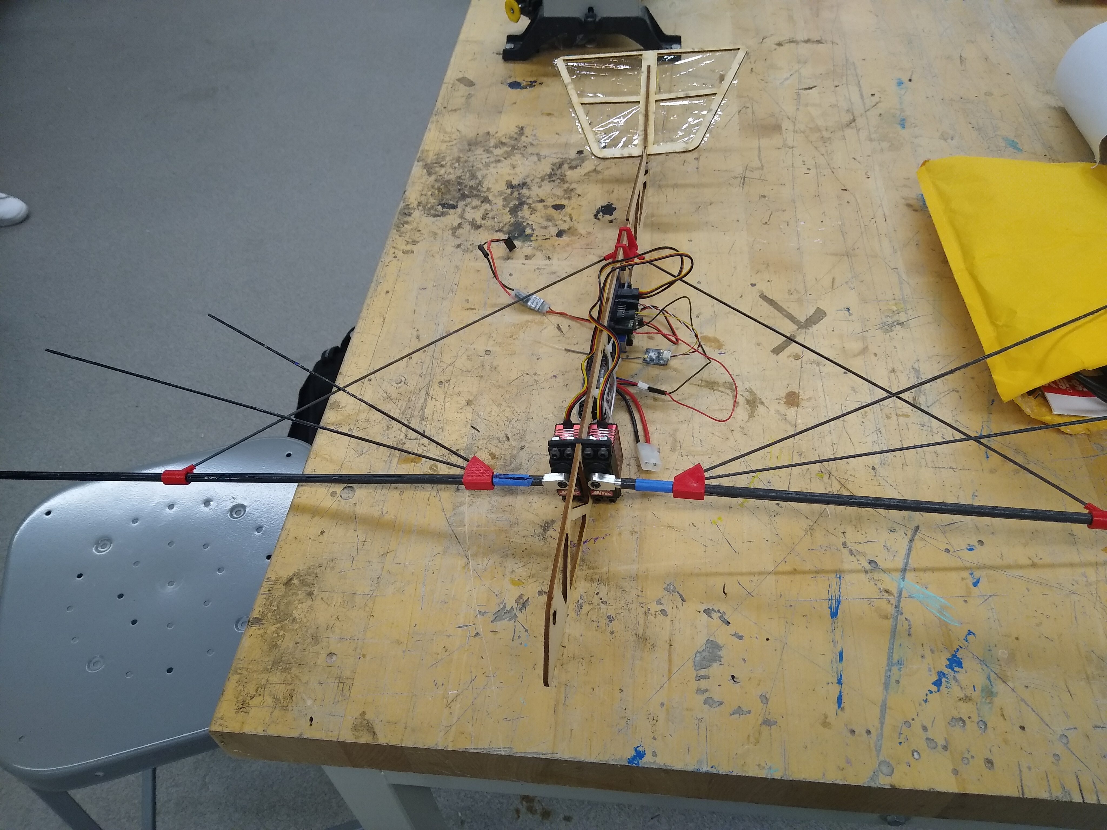
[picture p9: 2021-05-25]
images/spar-layout.jpg

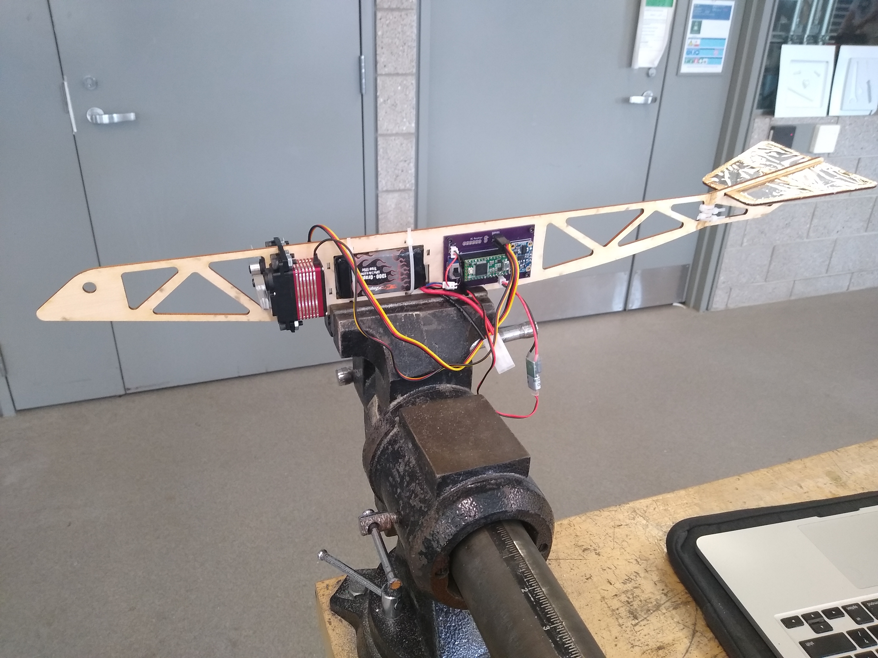
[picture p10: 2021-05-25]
images/ornithopter-body.jpg

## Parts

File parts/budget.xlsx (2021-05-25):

Item | Vendor | Quantity | Single Cost | Shipping + Tax | Total Cost | Status | Link
Total |  |  |  |  | $1958.17
Arduino Starter Kit | Arduino | 7 | $59 |  | $413.00 | Received | https://store.arduino.cc/usa/student-kit
Phoenix Ornithopter Kit | Gyroscope | 7 | $18.00 |  | $126.00 | Received | https://www.gyroscope.com/d.asp?product=PHOENIX
PVA Glue | Amazon | 2 | $7.50 |  | $15.00 | Received | https://www.amazon.com/Books-Hand-Neutral-Adhesive-spout/dp/B0025U109S
PVA Glue (2 pack) | Amazon | 3 | $10.50 |  | $31.50 | Received | https://www.amazon.com/Books-Hand-Neutral-Adhesive-spout/dp/B07X1V1ND4
Absolute Orientation Sensor | Adafruit | 2 | $34.95 |  | $69.90 | Received | https://www.adafruit.com/product/2472
Teensy 3.2 | Adafruit | 2 | $19.95 |  | $39.90 | Received | https://www.adafruit.com/product/2756
Flysky RC Transmitter and Reciever | Amazon | 1 | $45.69 |  | $45.69 | Received | https://www.amazon.com/Flysky-FS-i6X-Transmitter-FS-iA6B-Receiver/dp/B0744DPPL8
Servos | Servo City | 2 | $189.99 |  | $379.98 | Received | https://www.servocity.com/hsb-9370th-servo/?sku=39370S10
SPDT switch | Digikey | 2 | $4.13 |  | $8.26 | Received | https://www.digikey.com/en/products/detail/nidec-copal-electronics/8SS1022-Z/5086590
Jumper cables | Digikey | 1 | $1.95 |  | $1.95 | Received | https://www.digikey.com/en/products/detail/adafruit-industries-llc/1953/7241478
Custom servo arms | Birdkit | 2 | $9.95 |  | $19.90 | Received | http://www.birdkit.com/robotics.parts.html
DC/DC buck converter | Adafruit | 2 | $9.95 |  | $19.90 | Received | https://www.adafruit.com/product/1385
800mAh LiPo battery | Maxamps | 1 | $25.99 |  | $25.99 | Presumed lost | https://www.maxamps.com/lipo-800-2s-7-4v-heli-battery-pack
1300mAh LiPo battery | Maxamps | 1 | $29.99 |  | $29.99 | Received | https://www.maxamps.com/graphene-lipo-1300-2s-battery
LiPo battery charger | Amazon | 1 | $49.99 |  | $49.99 | Received | https://www.amazon.com/Charger-Professional-Balance-Multi-Functional-Intelligent/dp/B084CYCWNV
Wrapped carbon tubes | Goodwinds | 2 | $19.59 |  | $39.18 | Received | https://goodwinds.com/product/wct-sky-shark-3pt-32-5/
Carbon rods | Goodwinds | 4 | $7.99 |  | $31.96 | Received | https://goodwinds.com/product/cs-118-x-48-solid-round-carbon/
Duralar | Birdkit | 1 | $17.95 |  | $17.95 | Received | http://birdkit.com/robotics.duralar.html
2200mAh LiPo battery | Amazon | 1 | $11.99 |  | $11.99 | Received | https://www.amazon.com/EBL-Rechargeable-Batteries-Replacement-Electronics/dp/B087BYJ51T
Mini RC receiver | Amazon | 1 | $26.88 |  | $26.88 | Received | https://www.amazon.com/Flysky-FS-A8S-Receiver-i-BUS-Transmitter/dp/B0761N3FFC
Basswood | Midwest Products | 1 | $47.88 |  | $47.88 | Received | https://midwestproducts.com/collections/basswood/products/1-8x4x24-basswood-sheet-sku-4404
Custom PCB | OSH Park | 1 | $33.3 |  | $33.30 | Received | https://oshpark.com/ (custom board)
Durlar | Birdkit | 2 | $17.95 |  | $35.90 | Received | http://birdkit.com/robotics.duralar.html
Carbon fiber with foam core | DragonPlate | 1 | $360.00 |  | $360.00 | Received | https://dragonplate.com/carbon-fiber-prepreg-last-a-foam-core-sheet-0125-x-24-x-36
Absolute Orientation Sensor | Adafruit | 1 | $34.95 |  | $34.95 | Received | https://www.adafruit.com/product/2472
Ripstop nylon | Amazon | 1 | $8.95 |  | $8.95 | Received | https://www.amazon.com/EMMAKITES-Ripstop-Repellent-Dustproof-Airtight/dp/B00ZR81X56
Ripstop nylon | Amazon | 2 | $8.95 |  | $17.90 | Received | https://www.amazon.com/EMMAKITES-Ripstop-Repellent-Dustproof-Airtight/dp/B00ZR81X56
Ripstop tape | Amazon | 2 | $7.19 |  | $14.38 | Received | https://www.amazon.com/dp/B004ZLNG74?psc=1&ref=ppx_yo2_dt_b_product_details

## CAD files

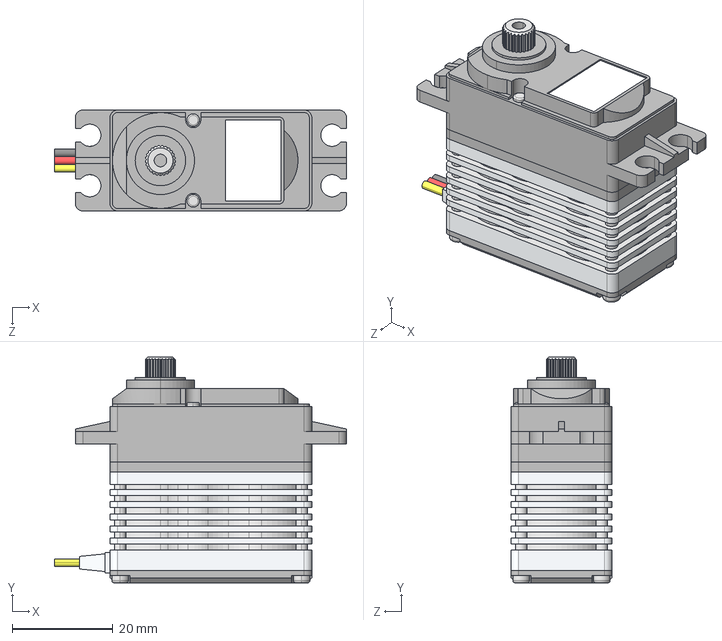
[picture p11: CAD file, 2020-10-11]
CAD/HSB-9380TH.STEP
57.9 x 44.8 x 20.0 mm

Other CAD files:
CAD/ornithopter.f3z

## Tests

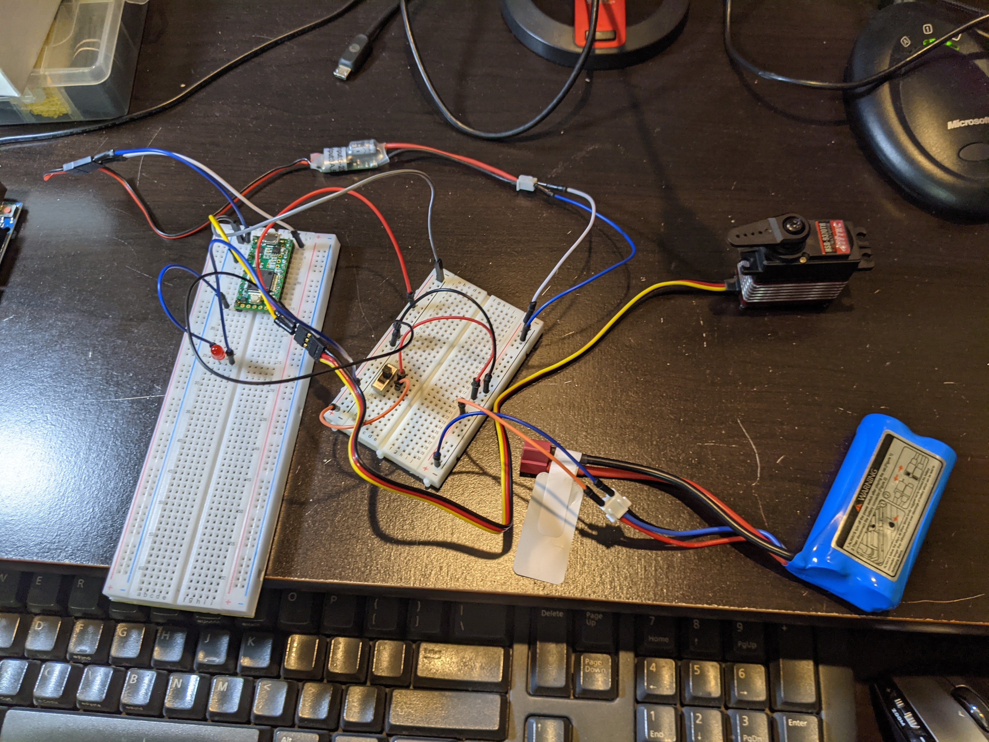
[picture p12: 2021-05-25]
images/testing-circuit.jpg

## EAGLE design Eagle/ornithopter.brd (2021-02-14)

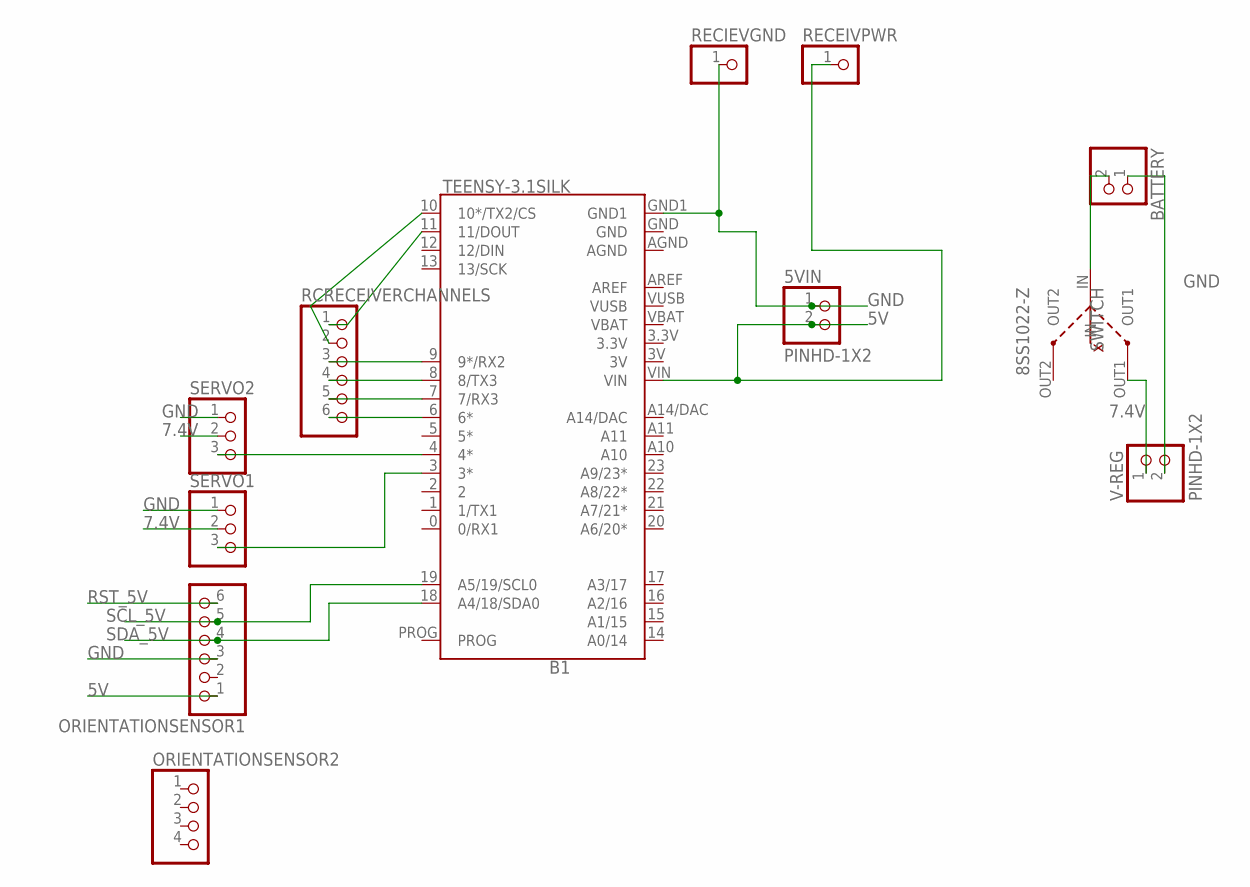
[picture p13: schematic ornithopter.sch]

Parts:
5VIN: PINHD-1X2; 1X02
B1: TEENSY-3.1SILK; TEENSY-3.1
BATTERY: PINHD-1X2; 1X02
ORIENTATIONSENSOR1: HEADER-1X676MIL; 1X06_ROUND_76
ORIENTATIONSENSOR2: HEADER-1X476MIL; 1X04_ROUND_76
RCRECEIVERCHANNELS: PINHD-1X6; 1X06
RECEIVPWR: PINHD-1X1; 1X01
RECIEVGND: PINHD-1X1; 1X01
SERVO1, SERVO2: PINHD-1X3CB; 1X03-CLEANBIG
SWITCH: 8SS1022-Z
V-REG: PINHD-1X2; 1X02

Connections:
3.3V: B1.3.3V
3V: B1.3V
5V: 5VIN.2, B1.VIN, ORIENTATIONSENSOR1.1, RECEIVPWR.1
7.4V: SERVO1.2, SERVO2.2, SWITCH.OUT1, V-REG.1
AGND: B1.AGND
GND: 5VIN.1, B1.GND, B1.GND1, BATTERY.1, ORIENTATIONSENSOR1.3, RECIEVGND.1, SERVO1.1, SERVO2.1, V-REG.2
unnamed: B1.11 (11/DOUT), RCRECEIVERCHANNELS.1
unnamed: B1.10 (10*/TX2/CS), RCRECEIVERCHANNELS.2
unnamed: B1.9 (9*/RX2), RCRECEIVERCHANNELS.3
unnamed: B1.8 (8/TX3), RCRECEIVERCHANNELS.4
unnamed: B1.7 (7/RX3), RCRECEIVERCHANNELS.5
unnamed: B1.6 (6*), RCRECEIVERCHANNELS.6
unnamed: B1.4 (4*), SERVO2.3
unnamed: B1.3 (3*), SERVO1.3
unnamed: BATTERY.2, SWITCH.IN
RST_5V: ORIENTATIONSENSOR1.6
SCL_5V: B1.19 (A5/19/SCL0), ORIENTATIONSENSOR1.5
SDA_5V: B1.18 (A4/18/SDA0), ORIENTATIONSENSOR1.4
VBAT: B1.VBAT
VUSB: B1.VUSB

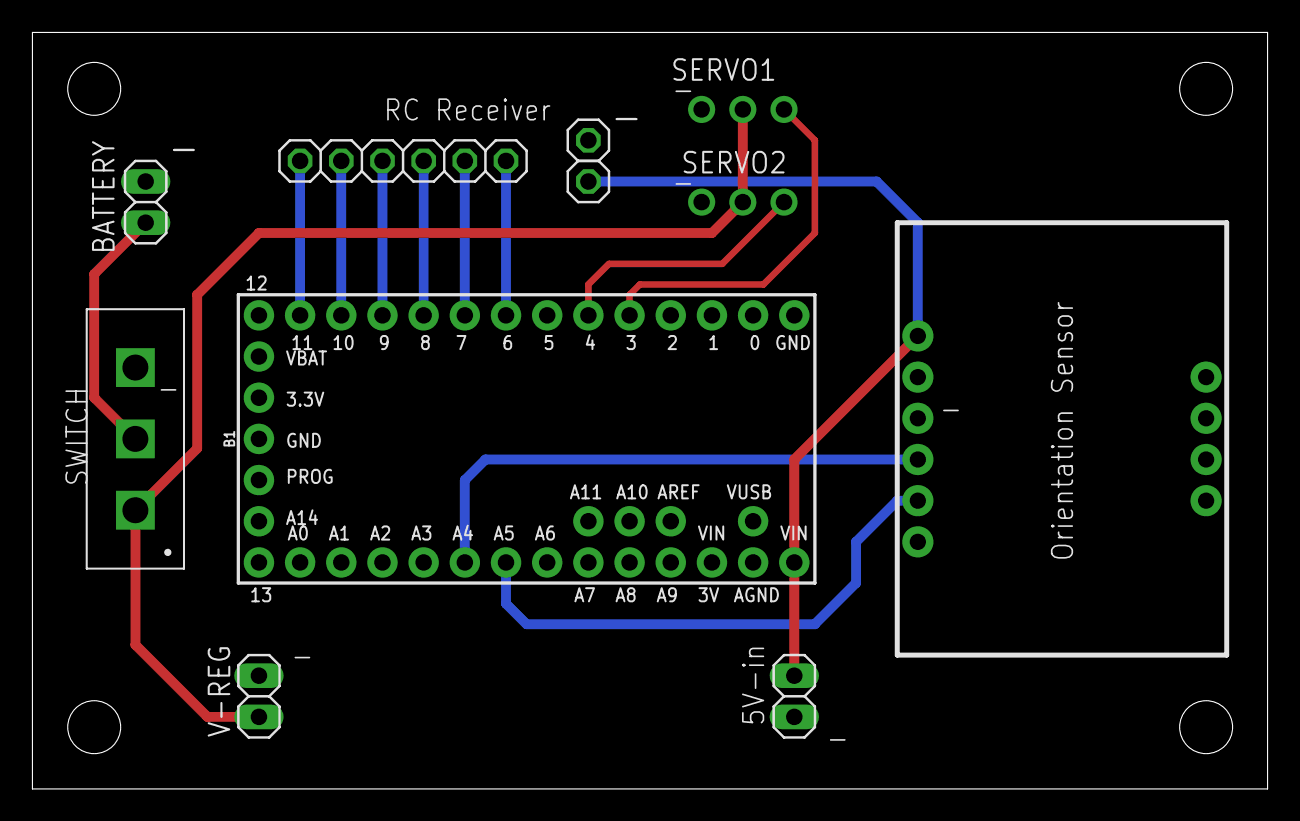
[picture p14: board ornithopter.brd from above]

Board: 2 copper layers, 76.2 x 46.7 mm, 12 parts (0 on the bottom side), 14 nets.

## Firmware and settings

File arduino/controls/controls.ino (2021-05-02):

#include <Servo.h>
#include <PulsePosition.h>

struct servoPair {
  Servo left;
  Servo right;
} wingServos;

// Define pins
int leftServoPin = 4;
int rightServoPin = 3;
int rxPin = 9;

// Initialize RC input
PulsePositionInput RCInput;

// RC controller channel mapping
const int RIGHT_VERTICAL = 1;
const int RIGHT_HORIZONTAL = 2;
const int LEFT_VERTICAL = 3;
const int LEFT_HORIZONTAL = 4;
const int LEFT_DIAL = 5;
const int RIGHT_DIAL = 6;
const int LEFT_SWITCH = 7;
const int RIGHT_SWITCH = 8;

// Define control modes
const int NORMAL_MODE = 1000;
const int BASIC_MODE = 1500;
const int AMP_MODE = 2000;

// User defined values
const float maxFrequency = 5; // Fastest flapping frequency
const int zeroThrottleAngle = 15; // Gliding angle when throttle is turned down
const int levelAngle = 0; // Angle at middle of flapping cycle
const int maxAmplitude = 45; // Maximum amplitude of flapping cycle
const int maxRollPhaseShift = 30; // Maximum phase shift in degrees when roll is at max
const int maxPitchAngle = 10; // Maximum change in angle when pitch is at max
const int maxYawAngle = 10; // Maximum change in angle when yaw is at max
const int deadZone = 50; // Range in which a control registers as a default value
const int delayTime = 5; // How fast in ms the loop cycles

// Initialize variables
int control_mode;
float throttle;
float roll;
float pitch;
float yaw;
float amp;

int startTime;
int elapsedTime;

float levelTheta;
float leftTheta;
float rightTheta;

struct pair {
  int left;
  int right;
} wings;

void updatePosition(float throttle, float roll, float pitch, float yaw, float amp) {
  if (throttle == 0) {
    wings.left = zeroThrottleAngle + pitch * maxPitchAngle + yaw * maxYawAngle;
    wings.right = zeroThrottleAngle + pitch * maxPitchAngle - yaw * maxYawAngle;
    return;
  }

  float deltaTheta = throttle * maxFrequency * ((float) delayTime / 1000) * 2 * PI;
  levelTheta += deltaTheta;

  if (roll < 0) {
    leftTheta = levelTheta;
    rightTheta = levelTheta + roll * maxRollPhaseShift * PI / 180;
  } else {
    leftTheta = levelTheta - roll * maxRollPhaseShift * PI / 180;
    rightTheta = levelTheta;
  }

  wings.left = levelAngle + maxAmplitude * amp * sin(leftTheta) + pitch * maxPitchAngle + yaw * maxYawAngle;
  wings.right = levelAngle + maxAmplitude * amp * sin(rightTheta) + pitch * maxPitchAngle - yaw * maxYawAngle;
}

void setup() {
  // Begin serial
  Serial.begin(9600);
  // Begin reading RC input
  RCInput.begin(rxPin);
  
  wingServos.left.attach(leftServoPin);
  wingServos.right.attach(rightServoPin);
  
  wingServos.left.write(90);
  wingServos.right.write(90);

  delay(1000);
  // Start clock
  startTime = millis();
}

// Normalize throttle readings
float normalize_throttle (float value) {
  if (value < 1000 + deadZone) {
    return 0;
  } else {
    return (value - (1000 + deadZone)) / (1000 - deadZone);
  }
}

// Normalizr steering readings
float normalize_steering (float value) {
  if (value < 1500 + deadZone && value > 1500 - deadZone) {
    return 0;
  } else if (value < 1500) {
    return (value - 1500 + deadZone) / (500 - deadZone);
  } else {
    return (value - 1500 - deadZone) / (500 - deadZone);
  }
}


void loop() {
  // Read RC input
  control_mode = RCInput.read(RIGHT_SWITCH);
  yaw = normalize_steering(RCInput.read(RIGHT_VERTICAL));
  pitch = normalize_steering(RCInput.read(RIGHT_HORIZONTAL));
  throttle = normalize_throttle(RCInput.read(LEFT_VERTICAL));

  if (control_mode == NORMAL_MODE) {
    roll = normalize_steering(RCInput.read(LEFT_HORIZONTAL));
    amp = normalize_throttle(RCInput.read(LEFT_DIAL));
  } else if (control_mode == AMP_MODE) {
    roll = normalize_steering(RCInput.read(LEFT_DIAL));
    amp = normalize_throttle(RCInput.read(LEFT_HORIZONTAL));
  } else if (control_mode == BASIC_MODE) {
    roll = 0;
    amp = 0.6;
  }
  
  updatePosition(throttle, roll, pitch, yaw, amp);

  wingServos.left.write(90 - wings.left);
  wingServos.right.write(90 + wings.right);

  delay(delayTime);
}

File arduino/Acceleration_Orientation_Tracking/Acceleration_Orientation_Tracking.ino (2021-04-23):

//things to code: isFalling, isFallingThreshold, getRotation, 
#include <Wire.h>
#include <Adafruit_Sensor.h>
#include <Adafruit_BNO055.h>
#include <utility/imumaths.h>

Adafruit_BNO055 bno = Adafruit_BNO055(55, 0x28);
imu::Vector<3> originalOrientation;
int defaultOrientation[3]={0,90,0};
imu::Vector<3> getEulerOrientation(){ //returns the euler orientation vector
  //create sensor event
  sensors_event_t event;
  bno.getEvent(&event);
  return(bno.getVector(Adafruit_BNO055::VECTOR_EULER));
}

float eulerToDegreeDifference(imu::Vector<3> standard){
  imu::Vector<3> newRotation = getEulerOrientation();
  int xdiff=(int)(standard.x()-newRotation.x())%180;
  int ydiff=(int)(standard.y()-newRotation.y())%180;
  int zdiff=(int)(standard.z()-newRotation.z())%180;
  
  float linearAcceleration = pow(pow(xdiff,2)+pow(ydiff,2)+pow(zdiff,2),0.5);
  if(linearAcceleration>90){
    return linearAcceleration-180;
  }else{
    return linearAcceleration;
  }
}

int getRollDiff(imu::Vector<3> standard, int isDefault=0){//returns the difference (in degrees) of the y euler angle
  imu::Vector<3> newRotation = getEulerOrientation();
  //convert angles to be between -180 and 180
  int adjNew=newRotation.y();
  int adjOld=standard.y();
  if(isDefault){
    adjOld=defaultOrientation[1];
  }
  
  int zdiff=(int)(adjNew-adjOld);

  

  if(zdiff>180)
    zdiff-=360;
  if(zdiff<-180)
    zdiff+=360;
  return zdiff;
}

int getPitchDiff(imu::Vector<3> standard, int isDefault=0){//returns the difference (in degrees) of the y euler angle
  imu::Vector<3> newRotation = getEulerOrientation();
  //convert angles to be between -180 and 180
  int adjNew=newRotation.y();
  int adjOld=standard.y();

  if(isDefault){
    adjOld=defaultOrientation[2];
  }
  
  int xdiff=(int)(adjNew-adjOld);
  if(xdiff>180)
    xdiff-=360;
  if(xdiff<-180)
    xdiff+=360;
  return xdiff;
}

void setup() {
  // put your setup code here, to run once:
  Serial.begin(115200);
  Serial.println("Orientation Sensor Test");

  if(!bno.begin())
  {
    /* There was a problem detecting the BNO055 ... check your connections */
    Serial.print("Ooops, no BNO055 detected ... Check your wiring or I2C ADDR!");
    while(1);
  }
  bno.setExtCrystalUse(true);

  //default orientation
  Serial.print("X:");
  Serial.print(defaultOrientation[0]);
  Serial.print("\tY:");
  Serial.print(defaultOrientation[1]);
  Serial.print("\tZ:");
  Serial.println(defaultOrientation[2]);

  Serial.print("Getting upright orientation data....");
  delay(1000);
  originalOrientation=getEulerOrientation();
  Serial.println("...Done!");
  
}

void loop() {
  // put your main code here, to run repeatedly:

  imu::Vector<3> orientation=getEulerOrientation();
  ///*
  Serial.print("X:");
  Serial.print(orientation.x());
  Serial.print("\tY:");
  Serial.print(orientation.y());
  Serial.print("\tZ:");
  Serial.println(orientation.z());
  //*/

  //original orientation
  /*
  Serial.print("X:");
  Serial.print(originalOrientation.x());
  Serial.print("\tY:");
  Serial.print(originalOrientation.y());
  Serial.print("\tZ:");
  Serial.println(originalOrientation.z());
  //*/
  //pitch and roll stuff
  /*
  Serial.print("Pitch Difference:");
  int pitchDifference=getPitchDiff(originalOrientation, 1);
  Serial.print(pitchDifference);
  Serial.print("\Roll Difference:");

  int rollDifference= getRollDiff(originalOrientation, 1);
  Serial.println(rollDifference);
  //*/
  //Serial.println(eulerToDegreeDifference(originalOrientation));

  
}

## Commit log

2020-10-11 Added files.
    [Adafruit_LSM6DSOX.brd, Adafruit_LSM6DSOX.sch, HSB-9380TH.STEP]
2020-10-30 Framework for gyro/wings/RC
2020-11-15 added motor control sketch
2021-01-10 Add files via upload
    1-10-2021 version, labeled and servo pins swapped with rc receiver
    [MainCircuitSchematic.brd]
2021-01-10 Add files via upload
    1-10-2021 schematic file
    [MainCircuitSchematic.sch]
2021-01-24 Add files via upload
    fixed receiver and servo pins
    [MainCircuitSchematic.brd]
2021-01-31 changed around files
    [Adafruit_LSM6DSOX.brd, Adafruit_LSM6DSOX.sch, MainCircuitSchematic.brd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]
2021-01-31 last updated 1/25/21
    [MainCircuitSchematic.brd, MainCircuitSchematic.sch]
2021-02-14 added switch to design, removed excess receiver pins
    [MainCircuitSchematic.brd, MainCircuitSchematic.sch]
2021-02-21 added throttle; test file for thursday
2021-02-26 comments, fixing organization, gyro updates
2021-03-24 added test file with two wings
2021-03-28 Update controls.ino
    Fixed directional controls
    [controls.ino]
2021-04-04 preliminary ornithopter sensor falling functions
2021-04-06 RC acts as on/off toggle for wings
2021-04-11 Update controls.ino
    Now with servos! :D
2021-05-25 Cleaned up files
    [MainCircuitSchematic.brd, MainCircuitSchematic.sch]
2021-05-25 Cleaning up files some more
    [Adafruit_LSM6DSOX.brd, Adafruit_LSM6DSOX.sch, MainCircuitSchematic.brd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]
2021-05-25 Added new files
    [budget.xlsx, ornithopter.brd, ornithopter.f3z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]

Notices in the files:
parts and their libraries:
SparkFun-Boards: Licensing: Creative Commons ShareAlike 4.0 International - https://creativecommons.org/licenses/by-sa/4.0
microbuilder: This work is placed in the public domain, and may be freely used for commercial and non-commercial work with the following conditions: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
